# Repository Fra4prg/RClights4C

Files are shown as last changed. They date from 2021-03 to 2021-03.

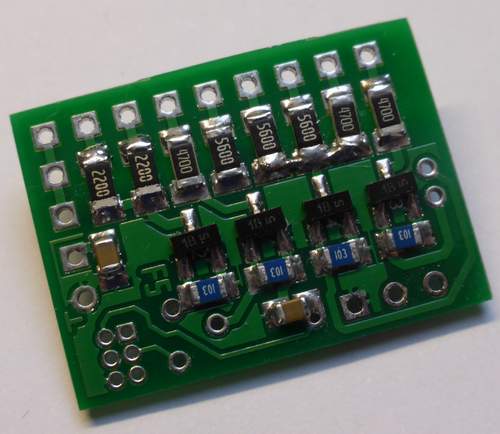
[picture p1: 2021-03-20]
pictures/PCB_bottom.JPG

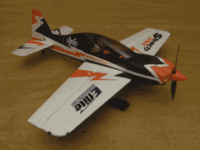
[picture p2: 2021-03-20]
pictures/RClights4C.gif

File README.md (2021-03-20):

# RClights4C
4 channel lightning module for RC models

The main controller electronic weighs only 1.4g and is populated on a 25 x 28 mm PCB.
In addition you need some wiring and LEDs depending on your configuration.
Enameled wire is the best choice for light weight models.
The module is suitable for big models as well as for ultra micro models such as planes, helicopters, ships, cars, ...

For RC control you only need one channel for controlling 4 independent output channels.
This is implemented as 16 discrete binaary coded channel values.
The RC channel can be mixed on the transmitter, e.g. from 4 switches.
The process how to do this is described in the documentation file (currently only in german).

The lightning patterns of eac output (number, length and pauses) can be programmed via transmitter.
E.g. you can use one channel for landing lights as permanent, another channel for strobe lights flashing 3 times every second, one for navigation lights and one for ACL lights.

If you don't have any free RC channel you can also connect a button to the RC input instead of an RC receiver.
With this you can switch through activating all 4 output channels subsequently.

RClights4C

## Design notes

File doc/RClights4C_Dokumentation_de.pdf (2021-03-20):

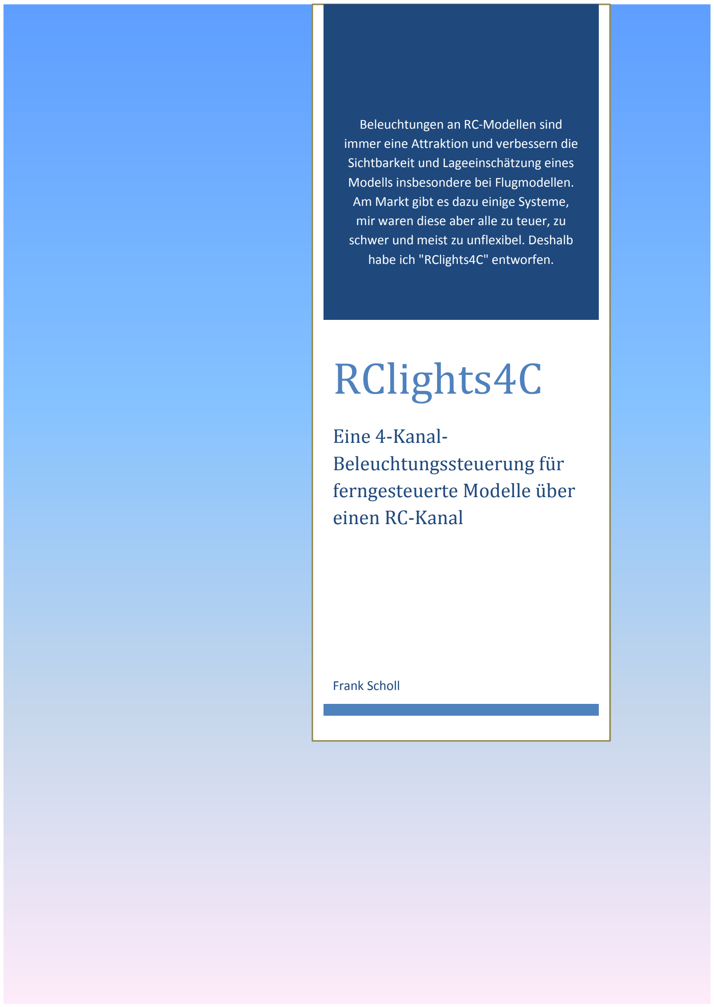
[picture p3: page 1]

Beleuchtungen an RC-Modellen sind immer eine Attraktion und verbessern die Sichtbarkeit und Lageeinschätzung eines Modells insbesondere bei Flugmodellen. Am Markt gibt es dazu einige Systeme, mir waren diese aber alle zu teuer, zu schwer und meist zu unflexibel. Deshalb habe ich "RClights4C" entworfen.

# RClights4C

## Eine 4-Kanal-Beleuchtungssteuerung für ferngesteuerte Modelle über einen RC-Kanal

Frank Scholl

Frank Scholl 26.01.2016

Dokumentation RClights4C 1

Einführung

Die eigentliche Steuerelektronik wiegt nur 1,4g und ist auf einer 25 x 28 mm großen Leiterplatte untergebracht. Dazu kommen noch je nach Wunsch einige LEDs und deren Zuleitungen, für die man am besten Lackdraht verwendet, sodass man meist bei 4-5g Gesamtgewicht landet. Damit ist die Steuerung sowohl für Großmodelle als auch für kleine Hallenflieger geeignet. Außer Flugmodellen lassen sich natürlich auch Schiffe, Autos oder was einem sonst so einfällt beleuchten.

Mit nur einem freien RC-Kanal lassen sich 4 unabhängige Beleuchtungs-Kanäle schalten. Möglich ist das durch 16 Stufen, die man binär codiert über Mischer am Sender auf 4 Schalter legt. Wie das genau funktioniert ist weiter unten beschrieben.

Die Leucht-Muster jedes der 4 Ausgänge, also die Anzahl der Lichtpulse, deren Dauer und Pausenzeiten lassen sich über den Sender ändern. So kann man z.B. einen Landescheinwerfer als Dauerlicht konfigurieren, die Anzahl und Länge der Strobe-Light-Blitze ändern oder die Art der Navigations- oder ACL-Lichter anpassen.

Hat man keinen freien Empfängerausgang zur Verfügung, kann man RClights4C alternativ auch über einen Taster steuern, den man statt des Empfängers anschießt. Damit lassen sich nacheinander alle 4 Kanäle ein- und wieder ausschalten.

Dokumentation RClights4C 2

Funktions-Prinzip

Die nachfolgende Skizze zeigt das Prinzip der Schaltung:

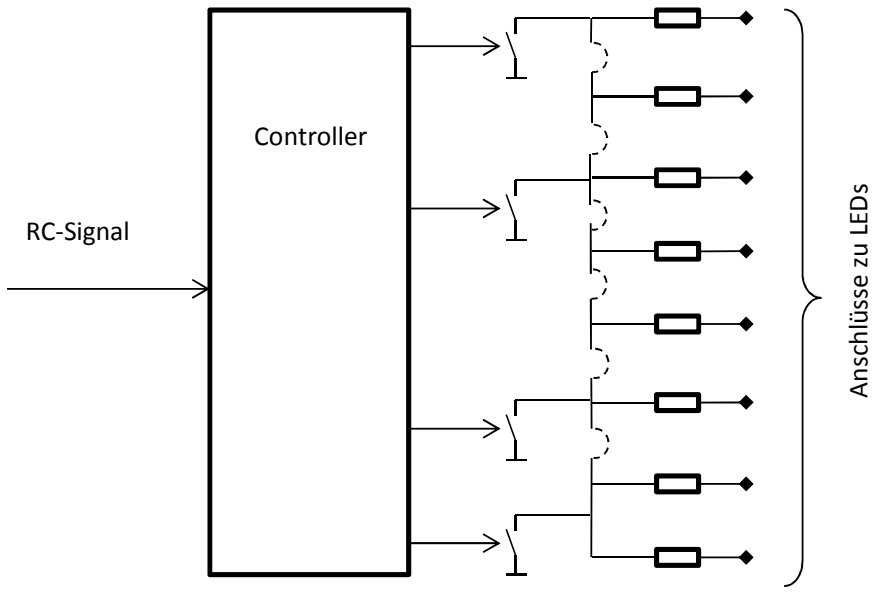
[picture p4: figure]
Anschlüsse zu LEDs; Controller; RC-Signal

Ein Controller decodiert das Signal eines RC-Empfänger-Ausgangs und schaltet 4 Ausgänge unabhängig voneinander gegen GND. Das RC-Signal wird dabei in 4 „Sub-Kanäle“ zerlegt, die jeweils einen Ausgangskanals aktivieren. Je nach Konfiguration kann der Ausgang permanent oder als Pulsfolge (Blink-Muster) geschaltet werden.

Dahinter liegen 8 Widerstände, die zu den LEDs führen. Im Gegensatz zu aufwändigeren Stromregelungsschaltungen, wie man sie in vielen käuflichen Steuerungen vorfindet, werden je nach Batteriespannung (1S-, 2S-, 3S-Lipo, …) LED-Farbe (unterschiedliche Flussspannungen!) und Anzahl in Reihe geschalteter LEDs unterschiedliche Widerstandswerte benötigt.

Die Ausgangsschalter können über Lötbrücken (gestrichelte Bögen) miteinander verbunden werden. So kann ein Schalter eine einzelne oder mehrere unterschiedliche LEDs bedienen. Die Schalter dürfen sogar untereinander verbunden werden, wenn man z.B. verschiedene Blinkmuster kombinieren oder den Ausgangsstrom erhöhen möchte.

Wegen dieser Konfigurationsmöglichkeiten kann eine Platine nicht so bestückt werden, dass sie alles abdeckt. Vielmehr bestimmen Batteriespannung, Art und Anzahl der LEDs was bestückt werden muss. Wie das bestimmt wird, ist weiter unten im Abschnitt „Auswahl der Widerstände“ beschrieben.

Prinzipschaltung

Dokumentation RClights4C 3

Beispiel-Konfiguration

Das UMX-Beast von Horizon-Hobby habe ich mit folgender Beleuchtung ausgestattet. Das ist vielleicht nicht ganz üblich für einen Doppeldecker, aber hier geht es hauptsächlich um den Spaßfaktor. Außerdem ist es sehr hilfreich für die Sichtbarkeit bei Dämmerung.

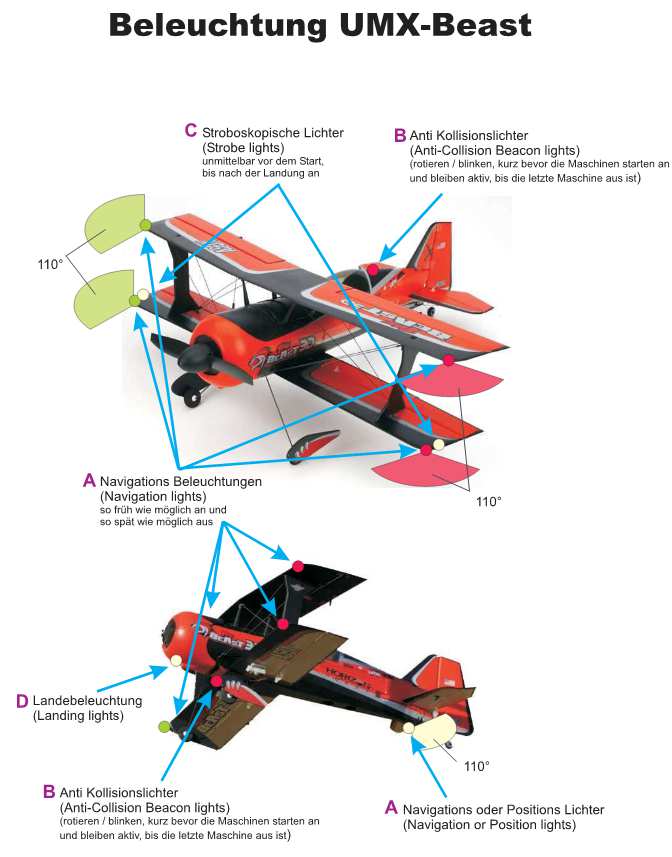
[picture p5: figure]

Dokumentation RClights4C 4

Luftfahrt-Vorschriften, Variationen

Bei Flugzeugen sind folgende Beleuchtungseinrichtungen vorgeschrieben:

- Navigations Beleuchtungen (Navigation lights)
Diese sollen so früh wie möglich an und so spät wie möglich ausgeschaltet werden.
Sie befinden sich an den Tagflächenenden und am Heck. Auf der rechten Seite sind sie grün, links rot und am Heck weiß.
Mit einem Abstrahlwinkel von 110° in der Ebene decken sie zusammen alle Seiten des Flugzeugs ab.
- Anti Kollisionslichter (ACL, Anti-Collision oder Beacon lights)
Diese roten Lichter rotieren oder blinken. Kurz bevor die Maschinen starten werden sie angeschaltet und bleiben aktiv, bis die letzte Maschine aus ist.
- Stroboskopische Lichter (Strobe lights)
Diese sollen erst unmittelbar vor dem Start angeschaltet werden, da sie das Bodenpersonal blenden können. Sei bleiben bis nach der Landung an.
- Landebeleuchtung (Landing lights)
Die Landescheinwerfer werden wie der Name schon sagt bei Start und Landeanflug eingeschaltet.

Siehe auch Links zu Informationen im Internet am Ende dieses Dokuments.

Dokumentation RClights4C 5

Einrichten des RC-Senders

Zur Ansteuerung muss der Sender so programmiert werden, dass über einzelne Schalter jeweils ein Ausgangskanal aktiviert wird.
Der verwendete Sender sollte dafür die Möglichkeit haben, 4 Schalter über Mischer frei auf einen Empfängerausgang zu programmieren. Bei weniger verfügbaren Schaltern lassen sich weniger Leuchtkanäle steuern.

Das RC-Signal aus dem Empfängerausgang, das per Definition eine Pulsbreite zwischen 1ms und 2ms hat, wird dazu in 16 Bereiche unterteilt.
Diese Bereiche werden im Sender als 0%..100% bzw. -100%..+100% angezeigt.

Der erste Schalter, der für den Ausgangskanal 1 zuständig ist, bestimmt ob die Pulslänge zwischen 1,0..1,5ms oder zwischen 1,5..2ms, also in der unteren oder oberen Hälfte der 16 möglichen Pulslängen liegt.
Der zweite Schalter für den Ausgangskanal 2, bestimmt ob die Pulslänge jeweils in der unteren oder oberen Hälfte der beiden durch Kanal 1 definierten Bereiche liegt, also zwischen 1,0..1,25ms bzw. 1,5..1,75ms oder zwischen 1,25..1,5ms bzw. 1,75..2,0ms.
Die beiden Schalter für die Ausgangskanäle 3 und 4 unterteilen die vorigen Bereiche in gleicher Weise nochmals. Somit entstehen diskrete 16 Signalbereiche.

Die folgende Tabelle zeigt das ganze etwas anschaulicher.
Der maximale RC-Puls-Bereich (hier 0,8..2,2ms - entsprechend +/- 125% eines Senderkanals) wird in 2

4
= 16 gleiche Zeitbereiche unterteilt (Spalte „RC-Puls“).
Schalter 1 am Sender bestimmt nun, ob die Pulslänge größer oder kleiner als 1,5ms ist also der Empfängerausgang ein Signal zwischen -125%..0% oder 0%..+125% liefert ( bzw.-25%..50% oder 50%..125% je nach Sendertyp), siehe rechte 2 Spalten.
| Schalter 1 | Schalter 2 | Schalter 3 | Schalter 4 | RC-Puls | Empfängerausgangssignal
| ungültig | ungültig | ungültig | ungültig | >2216 µs | Typ A | Typ B
16 | 1 | 1 | 1 | 1 | 1960-2208µs | 115,6% .. 125% | 109,3% .. 125%
15 | | | | 0 | 1896-1960µs | 106,2% .. 115,6% | 93,7% .. 109,3%
14 | | | 0 | 1 | 1832-1896µs | 96,8% .. 106,2% | 78,1% .. 93,7%
13 | | | | 0 | 1768-1832µs | 87,5% .. 96,8% | 62,5% .. 78,1%
12 | | 0 | 1 | 1 | 1704-1768µs | 78,1% .. 87,5% | 46,8% .. 62,5%
11 | | | | 0 | 1640-1704µs | 68,7% .. 78,1% | 31,2% .. 46,8%
10 | | | 0 | 1 | 1576-1640µs | 59,3% .. 68,7% | 15,6% .. 31,2%
9 | | | | 0 | 1512-1576µs | 50% .. 59,3% | 0% .. 15,6%
8 | 0 | 1 | 1 | 1 | 1448-1512µs | 40,6% .. 50% | -15,6% .. 0%
7 | | | | 0 | 1384-1448µs | 31,2% .. 40,6% | -31,2% .. -15,6%
6 | | | 0 | 1 | 1320-1384µs | 21,8% .. 31,2% | -46,8% .. -31,2%
5 | | | | 0 | 1256-1320µs | 12,5% .. 21,8% | -62,5% .. -46,8%
4 | | 0 | 1 | 1 | 1192-1256µs | 3,1% .. 12,5% | -78,1% .. -62,5%
3 | | | | 0 | 1128-1192µs | -6,2% .. 3,1% | -93,7% .. -78,1%
2 | | | 0 | 1 | 1064-1128µs | -15,6% .. -6,2% | -109,3% .. -93,7%
1 | | | | 0 | 800-1064µs | -25% .. -15,6% | -125% .. -109,3%
| ungültig | ungültig | ungültig | ungültig | <800 µs

Dokumentation RClights4C 6

Für jede der 16 möglichen Signalbereiche wird also eine bestimmte Kombination der Ausgänge aktiviert.

Beispiele:

- Bei [1] entsprechend -25% .. 15,6% bzw. -125% .. -109,3% sind alle Ausgänge ausgeschaltet.
- Bei [6] entsprechend 21,8% .. 31,2% bzw.-46,8% .. -31,2% ist Ausgang 1 aus, Ausgang 2 ein, Ausgang 3 aus und Ausgang 4 ein.
- Bei [16] entsprechend 115,6% .. 125% bzw. 109,3% .. 125% sind alle Ausgänge eingeschaltet.

Theoretisch könnte man noch eine weitere Unterteilung in 32 Bereiche vornehmen und damit das letzte verfügbare Pin des Controllers noch als weiteren Ausgang verwenden. Da anstatt eines externen Quarzes aber nur der interne Oszillator als Zeitbasis verwendet wird, der eine größere Toleranz hat, wurde darauf verzichtet. Bei zu feinen Unterteilungen kann es sein, dass sich Bereiche überschneiden und ein Kanal zu flackern beginnt.

Dokumentation RClights4C 7

Beispiel: Programmierung bei Graupner mc24

In diesem Beispiel schaltet der Schalter S1 den Ausgang 1 (Navi), S2 Ausgang2 (ACL), S3 Ausgang3 (Strobe) und S4 Ausgang4 (Landescheinwerfer).
Dazu werden folgende Mischer eingestellt:
| | | | L Mixanteil H | Offset
LinearMIX 1 | S 6 | S1 .\ | => | -50% | -50% | 0%
LinearMIX 2 | S 6 | S2 .\ | => | -25% | -25% | 0%
LinearMIX 3 | S 6 | S3 .\ | => | -13% | -13% | 0%
LinearMIX 4 | S 6 | S4 .\ | => | -6% | -6% | 0%
| Umk | Mitte | -Servoweg + | -Begrenz. +
Servo 6 | => | -6% | 125% | 125% | 125% | 125%
Die Änderung der Servomitte auf -6% bewirkt, dass das Signal immer etwa mittig in einem der 16 Signalbereiche liegt.

Beispiel: Programmierung bei Spektrum DX10t:

Hier wird ein 3-Stufen-Schalter (I) verwendet um Navi und ACL einzuschalten, zwei Einfach-Schalter (M, L) schalten Strobe und Landescheinwerfer ein. Der Ausgabekanal ist Fahrwerk bzw. Kanal5 (FW).

Mischer:
Mischer | | Schalter | Rate | Versatz
P-Mi x 1: | -I- > FW | EIN | 50% 100% | 0%
P-Mi x 2: | -M- > FW | EIN | 25% 100% | 0%
P-Mi x 3: | -L- > FW | EIN | 13% 100% | 0%

Servoeinstellung Ausgabekanal (hier FW)
| - Servoweg +
Servoweg | 125% | 125%
Sub Trim | +15
Die Änderung des Sub Trim auf 15 bewirkt, dass das Signal immer etwa mittig in einem der 16 Signalbereiche liegt.

Dokumentation RClights4C 8

Konfiguration der Lichtsignale über den RC-Sender

Der programmierte Controller ATtiny85 hat bereits eine Standard-Konfiguration:

- Kanal1 (über T4) schaltet bei Aktivierung dauerhaft ein. Das kann z.B. für die roten und grünen Navigationslichter an den Tragflächenenden verwendet werden.
- Kanal2 (über T3) gibt bei Aktivierung zwei Lichtpulse mit anschließender Pause aus. Das kann z.B. für die roten Anti-Kollisions-Lichter am Rumpf verwendet werden.
- Kanal3 (über T2) gibt bei Aktivierung einen kurzen Doppelblitz aus. Das kann z.B. für die weißen Stroboskop-Lichter an den Tragflächenenden verwendet werden.
- Kanal4 (über T1) schaltet bei wieder Aktivierung dauerhaft ein. Das ist für die Landescheinwerfer vorgesehen.

Darüber hinaus kann jeder Kanal aber auch individuell über den Sender programmiert werden.
Man wählt dabei zwischen Dauerlicht oder 1 bis 5 Lichtpulsen. Die Lichtpulse können eine Dauer T1 von einem der Werte aus Tabelle1 haben, die Pausen dazwischen T2 können Werte aus derselben Tabelle haben. Leuchtdauer und Pause sind aber unabhängig und müssen nicht gleich sein. Nach den Pulsen erfolgt dann eine Pause T3 mit Werten aus Tabelle3.
Wem das nicht reicht, der kann die Zeiten im Programm-Code in der Datei „RClights4C.c“ in den Feldvariablen „OntimeValues“ und „OfftimeValues“ ändern.

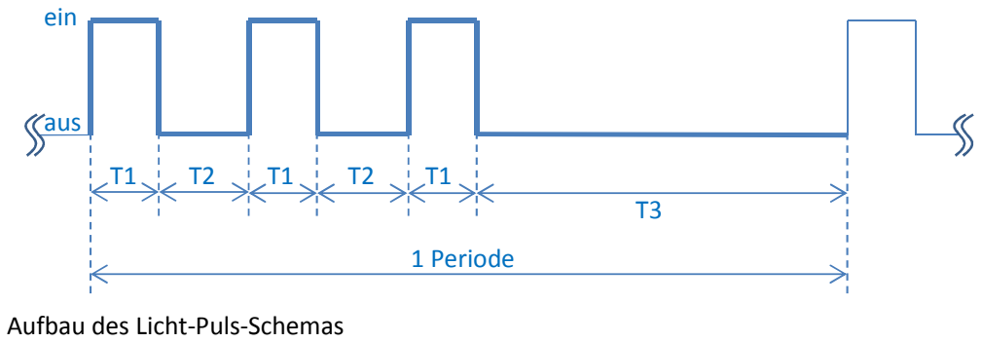
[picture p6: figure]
1 Periode; Aufbau des Licht-Puls-Schemas; ein; aus

Ich habe mich für die Vorgabe von festen Zeiten entschieden, da dies einfacher zu konfigurieren ist als freie Werte:

T1, T2
10ms
20ms
50ms
100ms
200ms
300ms
500ms
1000ms
Tabelle1:
Zeiten für Pulsdauer T1
und Pulspause T2

T3
0ms
10ms
20ms
50ms
100ms
300ms
500ms
1000ms
1500ms
2000ms
3000ms
Tabelle2:
Zeiten für Pause nach den Pulsen T3

Dokumentation RClights4C 9

Um die Werte der einzelnen Kanäle zu ändern ruft man das Setup-Menü auf.
Dazu geht man folgendermaßen vor:
1. Innerhalb der ersten 10 Sekunden nach Einschalten der Empfängerspannung den Schalter S1 (für Ausgangskanal 1) mindestens 5 Mal schnell ein- und ausschalten.
Bei Erfolg blitzen alle LEDs zweimal hintereinander auf.
Alle Schalter sollten jetzt in Stellung "aus" stehen.
2. Man kann jetzt den ersten Ausgangs-Kanal einstellen. Dieser gibt seine aktivierte Pulsform nun ständig aus. Alle anderen Kanäle sind ausgeschaltet.
Abhängig von der Stellung des Schalters S4 kann man nun mit S2 und S3 verschiedene Einstellungen des Kanals ändern:

Ist der Schalter S4 in Stellung "aus", dann

a. Ändert man durch ein- und ausschalten von S2 die Länge der Pulse T1.
b. Ändert man mit S3 die Pause T3 nach den Pulsen.
Wählt man mit S3 eine Pause von 0ms ist der Betrieb auf Dauerlicht eingestellt. Pulsdauer T1 und Pause T2 zwischen den Pulsen spielen dann keine Rolle mehr.

Ist der Schalter S4 in Stellung "ein", dann

c. Ändert man durch ein- und ausschalten von S2 die Anzahl der Pulse
d. Ändert man mit S3 die Pause T2 zwischen den Pulsen.
3. Ist an diesem Kanal alles wunschgemäß eingestellt, schaltet man mit S1 weiter zum nächsten Ausgangskanal.
Nach dem letzten Kanal wird das Setup verlassen und der Controller geht zum Normalbetrieb über.

Die eingestellten Pulsfolgen bleiben auch nach Ausschalten erhalten.

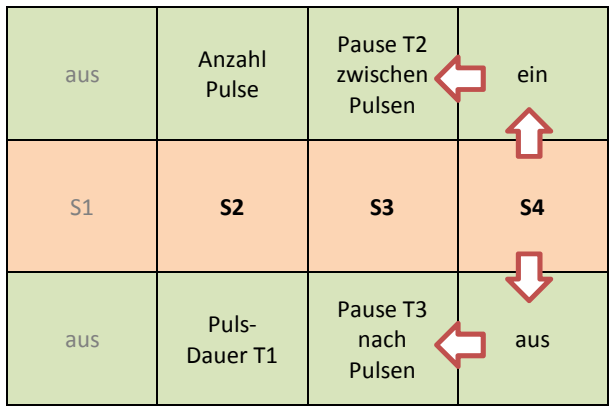
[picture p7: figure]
aus; Anzahl Pulse; Pause T2 zwischen Pulsen; ein; Puls-Dauer T1; Pause T3 nach Pulsen

Dokumentation RClights4C 10

Erläuterung der Schaltung

Kern der Schaltung ist ein 8-pinniger Atmel-Controller ATtiny85.
Dieser wertet das RC-Signal am Port PB2 aus und steuert über die Transistoren T1 bis T4 die externen LEDs an. Jeder Transistor BC846 kann bis zu 100mA Strom treiben, das reicht für gut 10 einzelne LEDs pro Kanal. Bei höheren Akkuspannungen kann man auch mehrere LEDs in Reihe schalten, das nutzt die Energie effizienter aus, kann aber dazu führen, dass die Helligkeit stärker mit dem Ladezustand schwankt.
Versorgt wird die Logik-Schaltung über den RC-Stecker X14 vom Empfänger. Dieser liefert 5V oder im Falle einer 1S-Lipo-Versorgung halt 3,3V..4,2V. Die LEDs versorgt man direkt aus der Batterie. Dazu dient der Verteiler X1, X2, X3, X4, X16. Bei 1S-Lipo-Versorgung entfällt diese Zusatzleitung, und man schließt VBATT mit VCC zusammen.
Die 8 Widerstände R1, R4, R6, R8, R11, R14, R15 und R16 bestimmen den Strom durch die an den 8 Anschlüssen X5, X6, X7, X8, X10, X11, X12 und X13. Sie müssen je nach LED-Farbe und –Typ und dem gewünschten Strom angepasst werden, siehe nächster Abschnitt.
Die Brücken B1 bis B6 sind auf der Leiterplatte zunächst nicht verbunden. Sie dienen dazu, mehrere Ausgangspins mit einem Kanal zu verbinden. Man schließt sie einfach mit Lötzinn. Lediglich X6 und X7 sind fest miteinander verbunden. Durch diese Brücken ist die Leiterplatte flexibler konfigurierbar. Die Pullup-Widerstände R19 bis R26 bleiben unbestückt. Sie sind nur für den Fall vorgehalten, dass hocheffiziente LEDs mal nicht ganz ausgehen und durch Leckströme der Transistoren oder Verunreinigungen auf der Platine weiterglimmen. Dann könnte man z.B. 10kOhm bestücken und das Nachglimmen sollte beseitigt sein.
Statt der Standard-Transistoren BC846 können auch Digital-Transistoren im SOT23-Gehäuse verwendet werden. Dann entfallen diePulldown-Widerstände R3, R7, R10 und R13 und die Basis-Widerstände R2, R5, R9 und R12 werden überbrückt.

Leiterplatten-Bestellung

Bei verschiedenen Leiterplattenherstellern kann man mit den fertigen Gerberdaten direkt bestellen. Das die Leiterplatte sehr klein ist, sind die Gerberdaten so erzeugt, dass man drei Leiterplatten am Stück bekommt, die man durch brechen oder fräsen vereinzeln kann.

Dokumentation RClights4C 11

Aufbau und Bestückung, Stückliste

Der Aufbau der Elektronik erfordert etwas Erfahrung beim Löten, immerhin sind SMD-Bauteile der Bauform 0805 nicht ganz so einfach zu handhaben. Wer sich das nicht selbst zutraut, kennt vielleicht jemanden, der ihn dabei unterstützt.
Für die Stückliste sind nur einige Bauteile generell festgelegt:
Designator | Wert | Bemerkung | Bauform | Menge
C1, C2 | 100nF | | 0805 | 2
R1, R4, R6, R8, R11, R14, R15, R16 | Werte nach Konfiguration | | 1206 8
R19, R20, R21, R22, R23, R24, R25, R26 | - | i.d.R. unbest. / ggf. 10k | 1206 | 8
R2, R3, R5, R7, R9, R10, R12, R13, R17, R18 | 10k | | 0805 | 10
T1, T2, T3, T4 | BC846B | | SOT-23 | 4
U1 | ATtiny85 | Low Power tinyAVR® 8-Bit Microcontroller, 4K Flash Memory, 10MHz | SOIC-8-L | 1
X15 | Pfostenstecker 2x3 1.27mm | Programmierung ISP6 | | 1
B1, B2, B3, B4, B5, B6 | Lötbrücke | je nach Konfiguration | | 6

Am besten ist es, wenn man den Controller vor der Bestückung in einem Adapter bereits programmiert. Dann kann der Programmierstecker X15 entfallen.

Auswahl der Widerstände

Die LED-Vorwiderstände R1, R4, R6, R8, R11, R14, R15 und R16 müssen je nach Akkuspannung und LED-Beschaltung individuell bestimmt werden.
Zur Vereinfachung habe ich die Excel-Tabelle „RClights4C.xlsx“ erstellt, mit der man die Widerstandswerte für alle Konfigurationen bestimmen kann. Die Tabelle ist geschützt, sodass man nur in den orange unterlegten Feldern Eintragungen vornehmen kann. Allerdings gibt es kein Passwort, man kann den Schutz also ggf. auch aufheben.
Wem das zu kompliziert ist, der findet vielleicht in einer der u.g. Beispiel-Konfigurationen schon etwas Passendes.
Zur Bestimmung der individuellen Widerstände geht man folgendermaßen vor:
- Schritt 1
Im Tabellenblatt „Widerstandswerte ermitteln“ trägt man die minimale, nominale und maximale Zellspannung des Akkus ein, bei Lipo-Akkus z.B. 3,0V/3,7V/4,2V.
Darunter die Anzahl der Zellen, bei einem 2S-Akku also „2“.
- Schritt 2
LEDs haben je nach Farbe und Typ unterschiedliche Flussspannungen. Die Werte entnimmt man den Datenblättern der verwendeten LEDs. Meist genügen aber die voreingetragenen Werte.

Dokumentation RClights4C 12

Außerdem gibt man hier an, mit welchem Strom die LEDs jeweils betrieben werden sollen.
Moderne, hocheffiziente LEDs sind schon bei wenigen mA sehr hell. Mit 5-10mA macht man i.d.R. aber nichts falsch.
Verwendet man die vorgegebenen Transistoren BC846, kann man die Werte für Imax und Usat belassen.
- Schritte 3, 4, 5
In den Spalten C, F, I und L wählt man für jeden Ausgang in den Zeilen 35, 38 usw. eine LED der gewünschten Farbe aus. Bei nur einer LED trägt man nur in Spalte C etwas ein, der Rest bleibt auf „n/a“. Will man 2 LEDs in Reihe schalten, wird auch in Spalte F etwas ausgewählt. Somit lassen sich bis zu 4 LEDs in Reihe schalten.
In Spalte Q der entsprechenden Zeile wird der empfohlene Widerstandswert berechnet. Da nicht alle berechneten Werte erhältlich sind, wählt man den nächst gelegenen Wert anhand der E-Reihen (oder aus den Werten des Bauteile-Händlers) und trägt diesen in Spalte S ein.
Spalte O gibt die Summe der LED-Flussspannungen an. Es versteht sich von selbst, dass diese Spannung kleiner sein muss, als die Akku-Spannung. Ist sie zu hoch, wird beim empfohlenen Widerstandswert ein Fehler angezeigt. In diesem Fall muss man weniger LEDs in Reihe schalten oder LEDs mit geringerer Flussspannung verwenden. Bei 1S-Akkus sind weiße und blaue LEDs wegen ihrer hohen Flussspannung eher ungeeignet.
Je höher die Differenz zwischen Akkuspannung und der Summe der LED-Spannungen ist, desto konstanter ist der Strom und damit die Leuchtstärke der LEDs über den Verlauf der Akku-Entladung. Allerdings steigt damit auch die Verlustleistung in den LED-Vorwiderständen. Diese wird zum verwendeten Widerstandswert bei voll geladenem Akku in Spalte W angegeben. Ist sie zu hoch (größer als 250mW) wird der Wert rot unterlegt. In diesem Fall kann man entweder mehr LEDs in Reihe schalten, eine kleinere Akkusspannung wählen oder einen zusätzlichen externen Widerstand dazwischen schalten.
- Schritt 6
In Spalte B, Zeilen 36, 39 usw. wählt man aus, ob die Brücke zwischen den Anschlüssen geschlossen ist. Sind alle Brücken geschlossen, dann überlagern sich die Signale aller Kanäle. Das ist zwar möglich und führt zu keiner Überlastung, dürfte aber wahrscheinlich selten gewünscht sein.
- Schritt 7
Schließlich sollte man die Stromwerte in den Feldern E62-E65 prüfen. Sind sie zu hoch, werden die Transistoren überlastet und es wird ein Fehler in der Splate F nebenan angezeigt.

Etwas Aufwand an dieser Stelle, dafür lässt sich die Steuerung aber sehr individuell an die jeweiligen Bedürfnisse anpassen.

Als LEDs können moderne hocheffiziente LEDs verwendet werden. Diese brauchen wenig Strom, haben aber meist einen kleinen Abstrahlwinkel, sodass sie nicht von allen Seiten gut sichtbar sind aber beim direkten Blick blenden können. Oft besser geeignet sind daher LEDs mit breitem Abstrahlwinkel und diffusem (opak) Körper.

Dokumentation RClights4C 13

Verdrahtungsbeispiele

Beispiel 1:
Akku = 1s (3,7V),
3x Navi, 2x ACL, 2x Strobe, 1x Landing
(siehe auch Tabellenblatt „Beispiel 1S“ in der Excel-Tabelle „RClights4C.xlsx“)

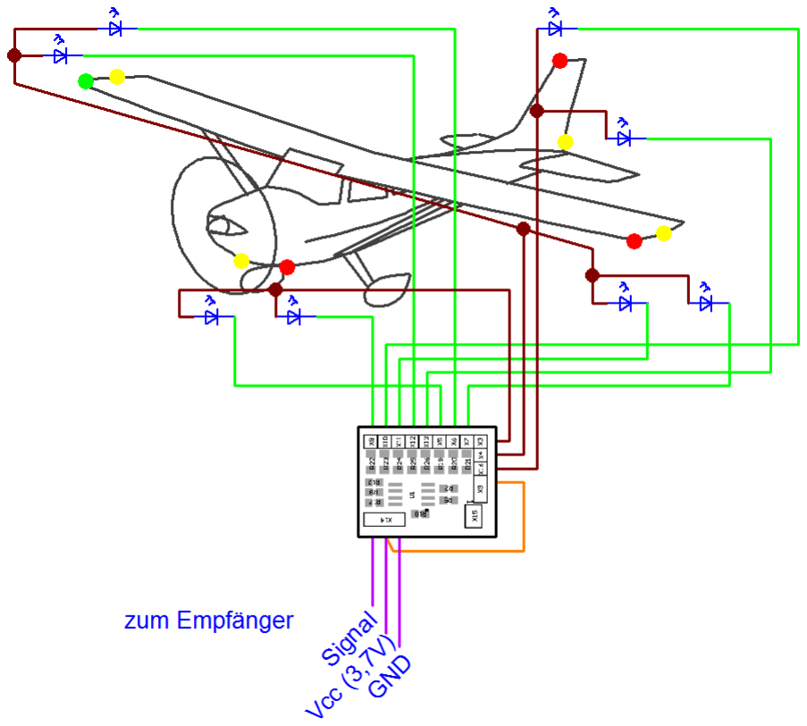
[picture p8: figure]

Die blauen LED-Schaltsymbole sind in der Nähe der bunt ausgefüllten Kreise dargestellt, die an der vorgesehenen Position am Flugzeugs dargestellt sind.
Die dunkelroten Leitungen stellen die Plus-Versorgung der LEDs an deren Anoden-Anschluss bereit. Bei 1S-Akkus können nicht mehrere LEDs in Reihe geschaltet werden, da die Spannung nicht ausreicht. Die grünen Leitungen führen die Kathoden-Anschlüsse zu den vorgesehenen Ausgängen der Elektronik.
Da bei 1S-Konfiguration die Spannung zur LED-Versorgung und zur Empfängerversorgung identisch sind, brauche wir keinen separaten Anschluss zum Pluspol des Akkus. Stattdessen muss aber über die orangefarbene Leitung eine Verbindung von X9-Pins 1 (dem Versorgungsanschluss aller LEDs) und der Empfänger-Versorgung an X14-Pin2 hergestellt werden. Somit reicht insgesamt ein Anschluß zum Empfänger aus.

Dokumentation RClights4C 14

Beispiel 2:
Akku = 2s (7,4V),
3x Navi, 2x ACL, 2x Strobe, 1x Landing
(siehe auch Tabellenblatt „Beispiel 2S“ in der Excel-Tabelle „RClights4C.xlsx“)

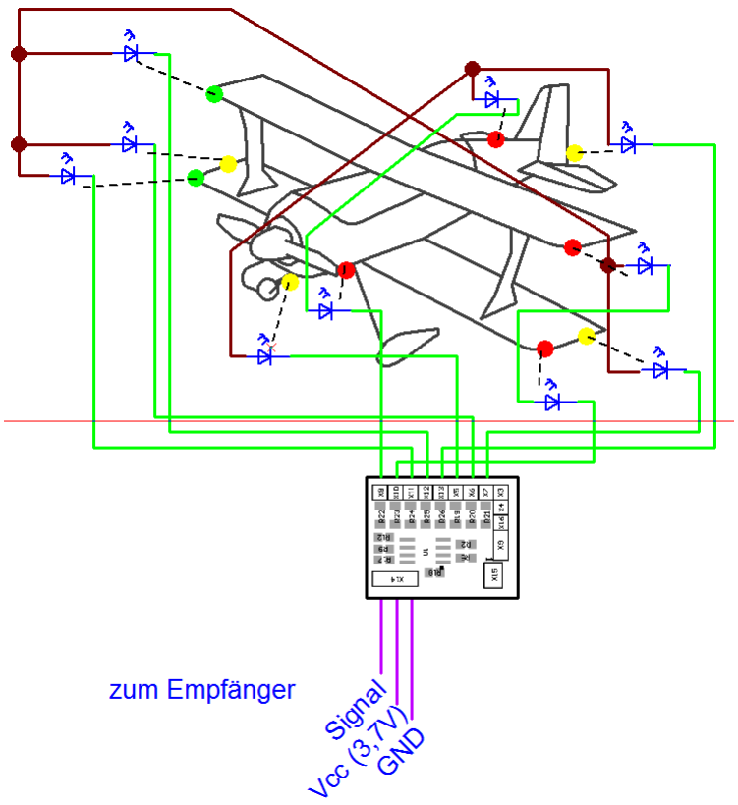
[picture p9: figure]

Die Leitungsfarben sind wie im Beispiel zuvor gewählt.
Bei 2S-Akkus kann man schon mal 2 LED in Reihe schalten.
Das hat den Vorteil, dass man bei gleichem Strom in einer Leitung mehr Licht bzw. mehr Leuchtpunkte erhält.

Dokumentation RClights4C 15

Beispiel 3:
Akku = 3s (11,1V),
2x Blinker rechts, 2x Blinker links, 2x Bremslichter, 2x Rücklichter, 2x Scheinwerfer (siehe auch Tabellenblatt „Beispiel 3S“ in der Excel-Tabelle „RClights4C.xlsx“)

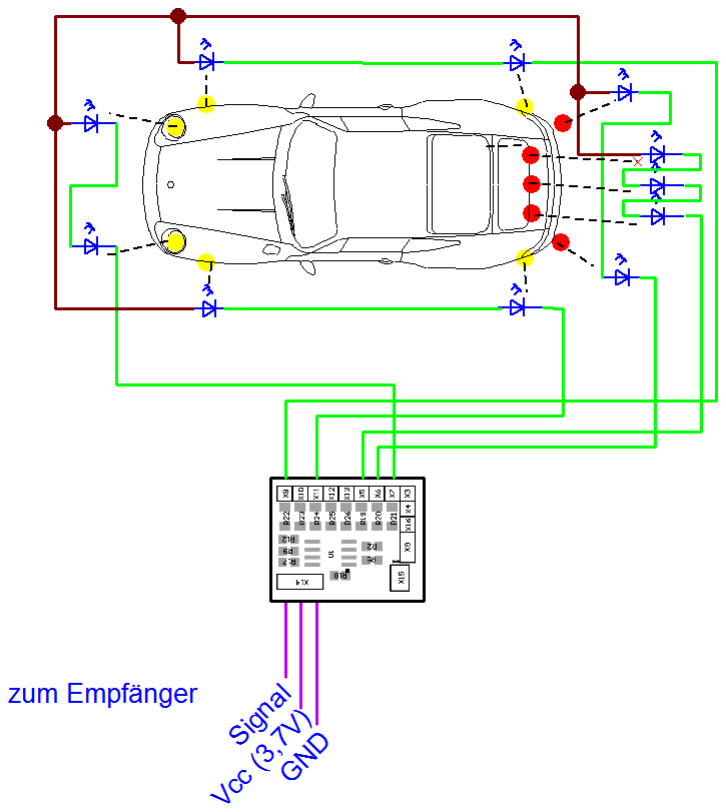
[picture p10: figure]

Als 3S-Beispiel habe ich der Abwechslung wegen mal ein Auto gewählt.
Bei 3S hat man schon mehr Möglichkeiten LEDs in Reihe zu schalten. Hier als Beispiel die 3 Bremsleuchten.
Es sind hier alle 4 Schaltfunktionen belegt, aber nur 5 Anschlüsse, da nur die Scheinwerfer und die Rücklichter auf einer gemeinsamen Funktion liegen.

Weitere Beispiele können mit Hilfe der Excel-Tabelle selbst berechnet werden.

Dokumentation RClights4C 16

Beschreibung der Programm-Struktur

Der Quellcode des Programms, das in der Programmiersprache C geschrieben wurde, ist hinreichend mit Kommentaren (in englischer Sprache) belegt, sodass hier nur eine grobe Programm-Beschreibung erfolgt.

Im Wesentlichen werden 2 Timer und ein Pin-Change-Interrupt verwendet.
Eine Flanke des RC-Signals löst einen Pin-Change-Interrupt aus. Bei steigender Flanke wird der Timer/Counter1 auf Null gesetzt, bei fallender Flanke wird die Pulsbreite über diesen Timer-Werte gemessen. Anschließend wird geprüft, ob der Wert einem gültigen RC-Signal entspricht.
Dieses wird dann durch einfache Bit-Operationen in 4 Unterkanäle zerlegt und der Aktivierungsstatus der entsprechenden Ausgangskanäle gesetzt.
Hier sieht man nun auch, warum der Pulsbereich von -125% bis +125%, also zwischen 0,8µs uns 2,2µs liegt: die Konfiguration des Timers und diese simplen Bit-Operationen passen genau zu diesem Pulsbereich. Wollte man den Pulsbereich auf -100% bis +100% legen, wäre der Programmieraufwand und die Laufzeit des Interrupts etwas höher, was ich mir hier erspart habe. Außerdem ist durch den größeren Bereich der Störabstand zwischen den möglichen diskreten Werten höher.

Liegt kein RC-Signal an, dann wird nach ca. 4ms ein Timer/Counter1 Overflow Interrupt ausgelöst und damit ein Timeout angezeigt. In diesem Interrupt, der dann ja ständig auftritt, wird auch ein Tastendruck, der eventuell statt des RC-Signals verwendet wird, ausgewertet und an das Hauptprogramm übergeben.

Der zweite Timer „Timer/Counter0“ wird nach jeder Millisekunde ausgelöst und steuert die Ausgänge an. Ist ein Ausgang aktiv, dann werden über verschiedene Zähler, die mit jeder Millisekunde hochgezählt werden, die Ein- und Ausschaltzeiten der Ausgangspulse abgearbeitet.
Die Längen der Pulse sind in den Tabellen „OntimeValues“ und „OfftimeValues“ abgelegt. Welcher Wert gewählt wurde, steht im EEPROM.

Das Hauptprogramm lässt zu Beginn alle LED-Ausgänge kurz aufblitzen Daran kann man dann erkennen, ob überhaupt alles funktioniert.
Anschließend aktiviert es bei einem erfolgten Tastendruck den nächsten Ausgangskanal.
Und es prüft, ob während der ersten 10 Sekunden nach Einschalten der Schalter S1 mehrfach hin und her geschaltet wurde. In diesem Fall wird das Setup-Programm aufgerufen, in dem man die Ausgabepulse ändern und im EEPROM ablegen kann.

Programm-Download

Zum Betrieb muss das Programm, das als fertige HEX-Datei vorliegt, in den Controller übertragen werden. Dazu gibt es verschiedene Möglichkeiten. In jedem Fall braucht man einen Programmier-Adapter für Atmel-Prozessoren, siehe Links im Anhang. Oder man kennt jemanden, der sowas schon einmal gemacht hat ☺
Der Controller kann auch bereits vor dem Einlöten programmiert werden. Dadurch erspart man sich auch das Gewicht des Programmiersteckers.

Bei den Fuse-Bits ist zu beachten, dass der interne Clock mit 8MHz gewählt wird und CKDIV8 deaktiviert ist. Außerdem sollte BODLEVEL=2V7 gesetzt sein.

Dokumentation RClights4C 17

Links
Der Autor
Homepage: | http://www.franx-funpage.de
Email: | megaprojects@t-online.de

Infos zu Atmel-Prozessoren und deren Programmierung:

http://www.lancos.com/prog.htmlhttp://www.mikrocontroller.net/articles/AVR-Tutorial

http://www.mikrocontroller.net/topic/117182

http://www.avr-asm-tutorial.net/avr_de/index.html

Eine Auswahl an Bauteil-Lieferanten:

http://www.reichelt.de/
http://www.pollin.de/

http://www.conrad.de/

Eine Auswahl an Leiterplattenherstellern:

https://docs.google.com/spreadsheet/ccc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

http://www.multi-circuit-boards.eu/

http://www.pcb-pool.com/

Eine Auswahl an Beschreibungen zur Beleuchtung von Flugzeugen:

http://de.wikipedia.org/wiki/Positionslichthttp://wiki.flightgear.org/De/Flugzeugbeleuchtung

http://www.ledprofishop.de/Flugzeugbeleuchtung-von-Piloten-erklaert

http://www.optotronix.de/hilfe/schnelleinfuhrung-in-die-modellflug-beleuchtung/

http://www.airliners.net/

Weitere Links:

http://www.fmt.de/

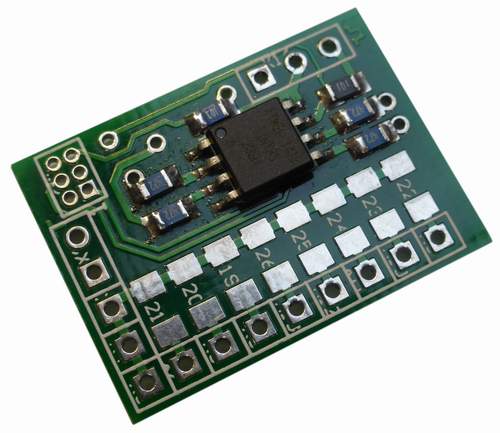
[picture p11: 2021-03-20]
pictures/PCB_top.JPG

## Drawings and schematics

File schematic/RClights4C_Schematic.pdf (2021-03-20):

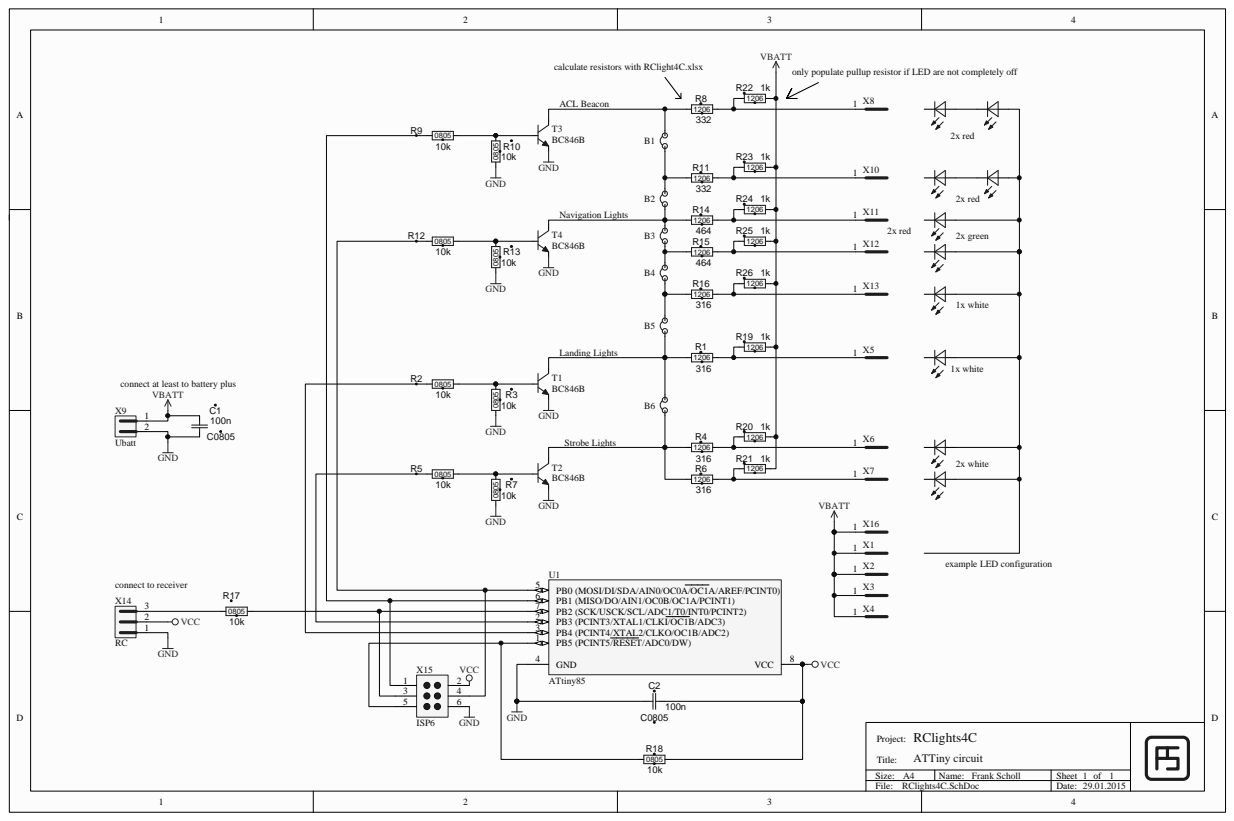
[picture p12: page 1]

connect at least to battery plus
VBATT

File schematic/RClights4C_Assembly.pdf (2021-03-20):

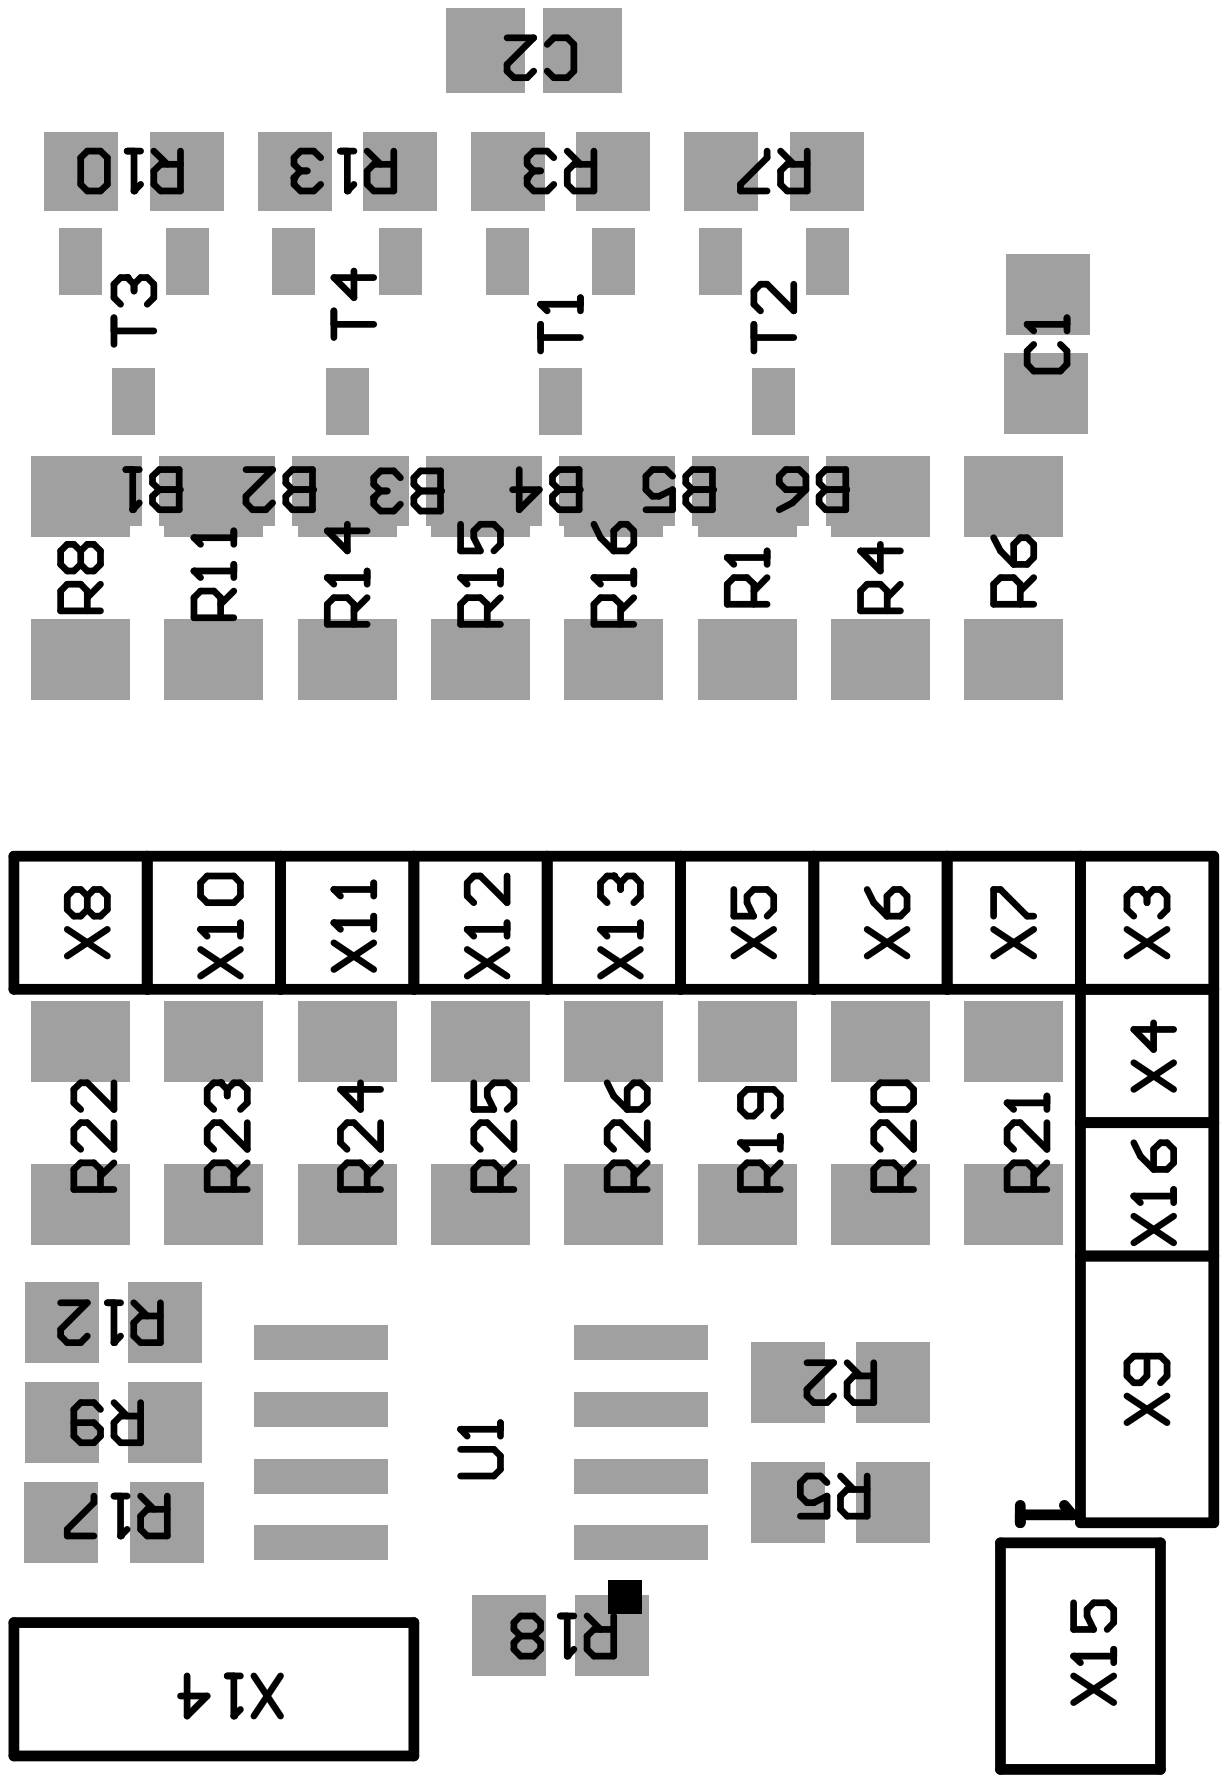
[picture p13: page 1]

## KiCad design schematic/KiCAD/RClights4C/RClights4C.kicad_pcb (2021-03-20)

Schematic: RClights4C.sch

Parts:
B1, B2, B3, B4, B5, B6: Jumper; SolderJumper-2_P1.3mm_Open_RoundedPad1.0x1.5mm
C2: 100n; C_0805_2012Metric
I1: ATtiny85-20SU; SOIJ-8_5.3x5.3mm_P1.27mm
R1, R4, R6, R8, R11, R14, R15, R16: 1k; R_1206_3216Metric
R17: 10k; R_0805_2012Metric
T1, T2, T3, T4: DTC114E; SOT-23
X1: Supply+; PinHeader_1x02_P2.54mm_Horizontal
X8: LEDs; PinHeader_1x08_P2.54mm_Horizontal
X9: Battery; PinHeader_1x02_P2.54mm_Horizontal
X14: RC; PinHeader_1x03_P2.54mm_Horizontal
X15: ISP; PinHeader_2x03_P1.27mm_Vertical

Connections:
+BATT: X1.1, X1.2, X9.1
/MISO: I1.6 (PB1), T3.1, X15.1
/MOSI: I1.5 (AREF/PB0), T4.1, X15.4
/RESET: I1.1 (~RESET~/PB5), X15.5
/SCK: I1.7 (PB2), R17.1, X15.3
GNDD: C2.2, I1.4 (GND), T1.2, T2.2, T3.2, T4.2, X9.2, X14.1, X15.6
unnamed: B1.1, R8.2, T3.3
unnamed: B1.2, B2.1, R11.2
unnamed: B2.2, B3.1, R14.2, T4.3
unnamed: B3.2, B4.1, R15.2
unnamed: B4.2, B5.1, R16.2
unnamed: B5.2, B6.1, R1.2, T1.3
unnamed: B6.2, R4.2, R6.2, T2.3
unnamed: I1.2 (XTAL1/PB3), T2.1
unnamed: I1.3 (XTAL2/PB4), T1.1
unnamed: R1.1, X8.6
unnamed: R4.1, X8.7
unnamed: R6.1, X8.8
unnamed: R8.1, X8.1
unnamed: R11.1, X8.2
unnamed: R14.1, X8.3
unnamed: R15.1, X8.4
unnamed: R16.1, X8.5
unnamed: R17.2, X14.3
VCC: C2.1, I1.8 (VCC), X14.2, X15.2

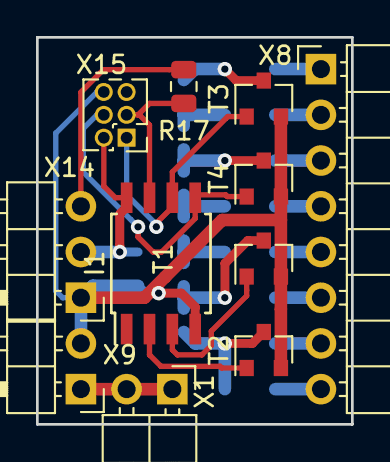
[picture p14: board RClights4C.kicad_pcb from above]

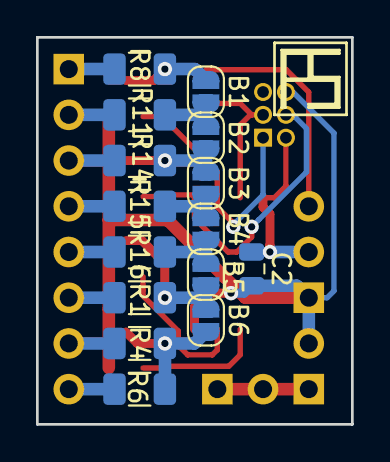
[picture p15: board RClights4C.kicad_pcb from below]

Board: 2 copper layers, 17.5 x 21.5 mm, 26 parts (15 on the bottom side), 25 nets.

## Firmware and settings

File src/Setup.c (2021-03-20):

/*------------------------------------------------------------------------------
 * Setup.c
 * generic initialisation routines for AeroLight_4C
 *
 * Copyright (c) 2014 Frank Scholl - MegaProjects@t-online.de
 *
 * ATTINY45 @ 8 MHz
 *
 * This program is free software; you can redistribute it and/or modify
 * it under the terms of the GNU General Public License as published by
 * the Free Software Foundation; either version 2 of the License, or
 * (at your option) any later version.
 *------------------------------------------------------------------------------
 */

 
 //  Include files
#include "all_headers.h"


/*------------------------------------------------------------------------------
 * Included Functions and ISR
 *  @details  -
 *  @param    -
 *  @return   -
 *------------------------------------------------------------------------------
 */

 
/*------------------------------------------------------------------------------
 * global variables
 *------------------------------------------------------------------------------
 */




/*------------------------------------------------------------------------------
 * Configure Ports (set direction)
 *  @details  -
 *  @param    -
 *  @return   -
 *------------------------------------------------------------------------------
 */
void config_ports (void)
{
	
	//Set Direction Registers (Input/Output) default set to Input (0x00) 
	//------------------------------------------------------------------
	
	// *** configure PORTB ***
	// Set output direction registers
	// PB.0 = (out, low)		LEDs for Navigation Lights
	// PB.1 = (out, low)		LEDs for ACL / Beacon
	// PB.2 = (in, Pullup)		RC signal
	// PB.3 = (out, low)		LEDs for Strobe Lights
	// PB.4 = (out, low)		LEDs for Landing Lights
	// PB.5 = (RESET in)
	//
	// Set input pullups
	PORTB = (0<<PB0)  | (0<<PB1)  | (1<<PB2)  | (0<<PB3)  | (0<<PB4)  | (0<<PB5);
	// Set directions
	DDRB  = (1<<DDB0) | (1<<DDB1) | (0<<DDB2) | (1<<DDB3) | (1<<DDB4) | (0<<DDB5);

}


/*------------------------------------------------------------------------------
 * Configure External Interrupts
 *  @details  -
 *  @param    -
 *  @return   -
 *------------------------------------------------------------------------------
 */
void config_extint (void)
{
	// *** MCU Control Register ***
	// SC01, ISC00: Interrupt Sense Control 0 Bit 1 and Bit 0
	//MCUCR = (0<<BODS) | (0<<PUD) | (0<<SE) | (0<<SM1) | (0<<SM0) | (0<<BODSE)  | (0<<ISC01)  | (0<<ISC00); // complete register
	//xxxxxxxxxxxxxxxxxxxxxxxxxxxxxxxxxxxxxxxxxxxxxxxxxxxxxxxxxx only change these bits (other bits used for different function)
	//                                               v            v          --> only bits used in this unit
	MCUCR = (MCUCR & ~((1<<ISC01) | (1<<ISC00))) | ((1<<ISC01) | (0<<ISC00));

	// *** GIMSK – General Interrupt Mask Register ***
	// INT0: External Interrupt Request 0 Enable
	// PCIE: Pin Change Interrupt Enable
	GIMSK = (0<<INT0) | (1<<PCIE); // complete register

	// *** GIFR – General Interrupt Flag Register ***
	// INTF0: External Interrupt Flag 0
	// PCIF: Pin Change Interrupt Flag
	//GIFR = (0<<INTF0) | (0<<PCIF); // complete register

	// *** PCMSK – Pin Change Mask Register ***
	// PCINT5:0: Pin Change Enable Mask 5:0
	PCMSK = (0<<PCINT5) | (0<<PCINT4) | (0<<PCINT3) | (1<<PCINT2) | (0<<PCINT1) | (0<<PCINT0); // complete register


}


/*------------------------------------------------------------------------------
 * setup uC
 *  @details  -
 *  @param    -
 *  @return   -
 *------------------------------------------------------------------------------
 */
void setup (void)
{	
	//Init uC peripheral
	//-------------------
	config_ports();			// this configures the I/O ports

	TimerInit();
	
	config_extint();

	// reset button detection (set by 4ms timeout)
	button_release_count = 0;
	button_pressed_count = 0;
	button_was_read = true;
	button_state = BUTTON_NOT_AVAILABLE;

		
		// *** get saved values from EEPROM ***

//		flash(0b10000000, 10, 20, 50, false);  // =====================
//		long_delay_ms(1000);

/* compare complement does not work at first instance !!!!!!!!!!!!!?????????
		rd_EE = eeprom_read_byte(&EE_pattern_select);
		rd_EE_cp = eeprom_read_byte(&EE_pattern_select_cp);
		if (rd_EE == (~rd_EE_cp))  // check redundancy by complement
		{
			check=0; // dummy
		}


//		flash(0b10000000, 10, 20, 50, false);  // =====================
//		long_delay_ms(1000);

		LEDspeed = constrain(eeprom_read_byte(&EE_LEDspeed),SPEED_MIN,SPEED_MAX);
		eeprom_write_byte ( &EE_LEDspeed, LEDspeed);
		eeprom_write_byte ( &EE_LEDspeed_cp, ~LEDspeed);
*/

		// enable interrupts
		sei();
		
//		long_delay_ms(100);
}

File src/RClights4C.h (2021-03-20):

/*------------------------------------------------------------------------------
 * RClights_4C.h
 * main for AeroLight_4C
 *
 * Copyright (c) 2015 Frank Scholl - MegaProjects@t-online.de
 *
 * ATtiny85
 *
 * This program is free software; you can redistribute it and/or modify
 * it under the terms of the GNU General Public License as published by
 * the Free Software Foundation; either version 2 of the License, or
 * (at your option) any later version.
 *------------------------------------------------------------------------------
 */


#ifndef _MAIN_H
#define _MAIN_H

 /*------------------------------------------------------------------------------
 * definitions
 *------------------------------------------------------------------------------
 */

#define LEDS_PORT		PORTB	// Port for LEDs
#define LEDS_PORT_RD	PINB	// Port for LEDs
#define LED_NAVI		PB0		// LEDs for Navigation Lights
#define LED_ACL			PB1		// LEDs for ACL / Beacon
#define LED_STROBE		PB3		// LEDs for Strobe Lights
#define LED_LAND		PB4		// LEDs for Landing Lights

#define RC_PORT_RD		PINB	// Port for RC signal
#define RC_PIN			PB2		// Pin for RC signal

#define RCPULSE_MIN			 63		// minimum decoded RC pulse  63*16µs = 1008µs
#define RCPULSE_MAX			126		// minimum decoded RC pulse 126*16µs = 2016µs
#define RCPULSE_MINLIMIT	 50		// minimum valid   RC pulse  50*16µs =  800µs
#define RCPULSE_MAXLIMIT	138		// minimum valid   RC pulse 138*16µs = 2208µs

#define NUMBER_OF_CHANNELS 4	// do not change this. ATtiny85 can only handle up to 4 LED channels
/*
#define NAVI   0	// channel number for navi lights
#define ACL    1	// channel number for ACL lights
#define STROBE 2	// channel number for strobe lights
#define LAND   3	// channel number for landing lights
*/

// variables for used light patterns
typedef struct {
	bool		active;				// indicates that channel is activated
	uint8_t		ontime;				// index to table OntimeValues[] with values for LED on (each pulse) time in ms if activated
	uint16_t	ontimecount;		// counter for LED on time per pulse in ms
	uint8_t		offtimepulse;		// index to table OfftimeValues[] with values for LED off time between pulses in ms, 0=permanent on if activated
	uint16_t	offtimepulsecount;	// counter for LED off time between pulses in ms
	uint8_t		offtime;			// index to table OfftimeValues[] with values for LED off time after pulses in ms, 0=permanent on if activated
	uint16_t	offtimecount;		// counter for LED off time after pulses in ms
	uint16_t	timecount;			// counter for LED on/off  time in ms
	uint8_t		pulses;				// number of light pulses interrupted by offtimepulse until last offtime
	uint8_t		pulsecount;			// counter for pulses within 1 period
	uint8_t		ledpin;				// portpin where channel LED is connected to
} LightControl_t;

typedef struct {
	uint8_t		ontime;				// index to table OntimeValues[] with values for LED on (each pulse) time in ms if activated
	uint8_t		offtimepulse;		// index to table OfftimeValues[] with values for LED off time between pulses in ms, 0=permanent on if activated
	uint8_t		offtime;			// index to table OfftimeValues[] with values for LED off time after pulses in ms, 0=permanent on if activated
	uint8_t		pulses;				// number of light pulses interrupted by offtimepulse until last offtime
	uint8_t		ledpin;				// portpin where channel LED is connected to
} LightControl_Def_t;

/*------------------------------------------------------------------------------
 * Macro definitions
 *------------------------------------------------------------------------------
 */
//#define sbi(port,bit)  (port |= (1<<bit))   //set bit in port
//#define cbi(port,bit)  (port &= ~(1<<bit))  //clear bit in port

// Contrain() macro from Arduino:
#define constrain(amt,low,high) ((amt)<(low)?(low):((amt)>(high)?(high):(amt)))

/*------------------------------------------------------------------------------
 * FLASH constants
 *------------------------------------------------------------------------------
 */

/* list of time values [ms] for ontime parameter of a channel */
#define LEN_ONTIMEVALUES 8
extern const uint16_t OntimeValues[LEN_ONTIMEVALUES] PROGMEM;

/* list of time values [ms] for offtime parameter of a channel */
#define LEN_OFFTIMEVALUES 11
extern const uint16_t OfftimeValues[LEN_OFFTIMEVALUES] PROGMEM;


/*------------------------------------------------------------------------------
 * global variables
 *------------------------------------------------------------------------------
 */

extern volatile uint8_t		timecount_RCpulse;	// counter for RCpulse, 1 tic = 16,00µs
extern volatile bool		RCpulse_timeout;	// timed out on Timer overflow
extern volatile bool		RC_subch1;			// RC signal value subchannel 1
extern volatile bool		RC_subch2;			// RC signal value subchannel 2
extern volatile bool		RC_subch3;			// RC signal value subchannel 3
extern volatile bool		RC_subch4;			// RC signal value subchannel 4

extern volatile uint8_t button_release_count;	// 4ms timout counter for released button
extern volatile uint8_t button_pressed_count;	// 4ms timout counter for pressed button
extern volatile uint8_t button_state;			// show button state
#define BUTTON_NOT_AVAILABLE	0				// value for button state
#define BUTTON_PRESSED			1				// value for button state
#define BUTTON_RELEASED			2				// value for button state
extern volatile bool button_was_read;			// report button read state

extern volatile LightControl_t LightChannel[NUMBER_OF_CHANNELS];	// array pattern configurations per channel


// no 'volatile' qualifier for pointer target type
extern uint8_t    EE_pattern_select;		// saved pattern
extern uint8_t    EE_pattern_select_cp;		// saved pattern complement
extern uint8_t    EE_LEDspeed;				// saved LED speed
extern uint8_t    EE_LEDspeed_cp;			// saved LED speed complement


/*------------------------------------------------------------------------------
 * used functions
 *------------------------------------------------------------------------------
 */
//extern void switch_LED(uint8_t, uint8_t);
extern void flash (uint8_t, uint8_t, uint16_t, uint16_t, bool);


#endif //_MAIN_H

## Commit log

2021-03-20 Initial update
    [RClights4C.kicad_pcb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]
2021-03-20 3x panel added
    [AL_SMD_3x.GBL, AL_SMD_3x.GBO, AL_SMD_3x.GBS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]
